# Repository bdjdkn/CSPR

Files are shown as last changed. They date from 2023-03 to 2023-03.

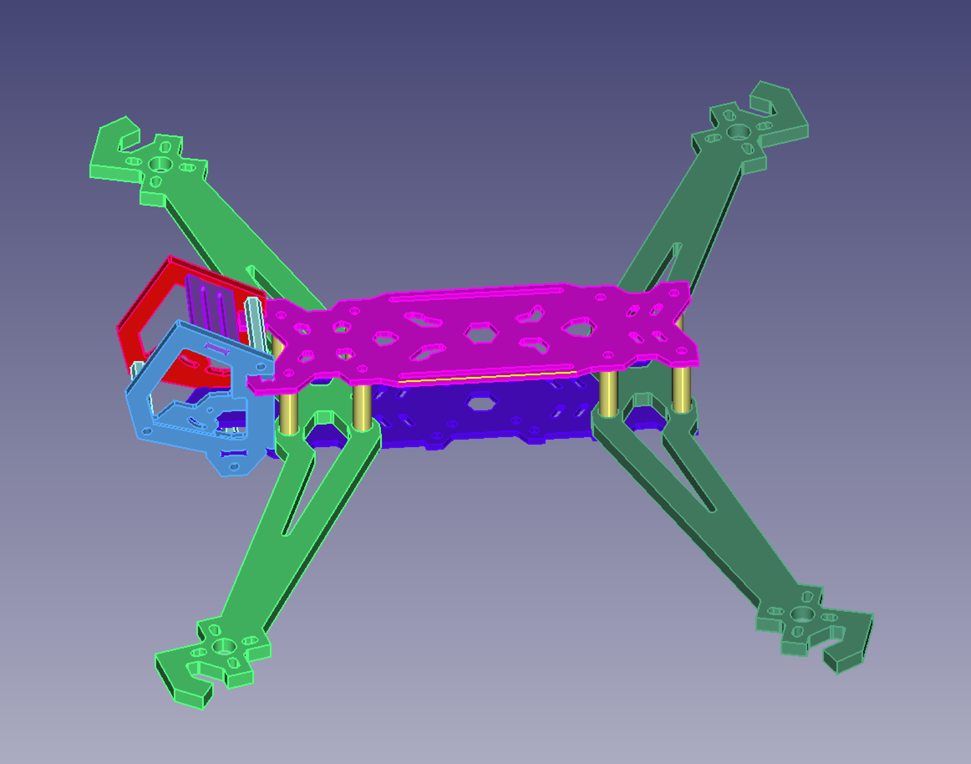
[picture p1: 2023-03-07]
图纸与模型/模型/动平台四代/参考资料/iflight-hl7-1.snapshot.7/2.png

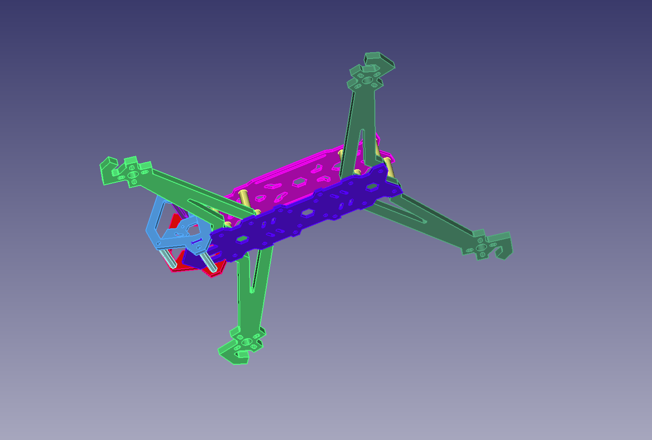
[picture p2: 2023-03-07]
图纸与模型/模型/动平台四代/参考资料/iflight-hl7-1.snapshot.7/3.png

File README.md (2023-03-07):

# CSPR
a machine with rope_driven  
这是一个四电机四卷筒的绳驱动系统，包含了机械设计部分和控制性文件，还在更新中，尚未完成  
This is a system which is combine with four rolls,the repository included the design of machine and part of controling code.the project is still updating  
RECODE  
22_6 creat the project and start to design  
22_12 finished the machine design and start to design the software  
23_2 finished the combine of the machine

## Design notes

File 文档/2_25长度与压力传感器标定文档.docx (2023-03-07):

# 长度与压力标定

1、 长度标定

目的：测量长度与卷筒旋转角度的关系，是否符合设计需求

测量方法：使用DJI Assistant软件位置环控制电机。

1、 上电前双手拉紧绳子，使卷筒保持初始位置。
2、 上电并使用PWM接口，杜邦线带金属眼端朝上插入FT232芯片的串口转换器
3、 打开DJI Assistant1.9软件，软件将识别电机，进入控制模式
4、 更改为位置环控制，电机将上电初始位置设置为0点
5、 确保电机出于0点位置，并使绳子稍微绷紧（过大的力量将会改变卷筒位置），并使用软件让电机转动一圈
6、 用记号笔在出绳点附近的绳上涂抹一端
7、 使用控制软件让电机转回一圈
8、 稍微绷紧绳子，观察电机数据，保持0点
9、 测量出绳点到记号的距离并记录
10、 同样的方法测量半圈的长度，并记录

测量数据：

出绳标号 | 一圈数据（理想为502.65mm） | 半圈数据（理想为251.32mm）
B1-1
B1-2
B2-1
B2-2
B3-1
B3-2
B4-1
B4-2

2、 压力标定

目的：校准压力传感器，减少偏差

测量方法：

1、 打开MATLAB setting_2_4
2、 依据软件提示完成配置
3、 打开simulink real_time_2_4
4、 测试不同重量下的读书，是否准确

Ps：标定零点时要确保绳子处于伸直状态且无重物挂载，标定选择对的通道，且重物稳定不晃动

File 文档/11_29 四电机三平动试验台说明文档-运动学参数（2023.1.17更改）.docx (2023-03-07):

# 四电机三平动试验台说明文档

编写人：项升 张胤启 22/11/30

文档使用软件：绘图Visio AxGlyph 公式 Axmath

2023/1/17 进行完善，更改了运动学参数和图片，完善了电气布置

## 1运动学参数和零件编号

下图1-1采取从控制电脑向架子（向北视角），对1）电机can地址拨码编号，贴纸（1-7， 现有电机为1-4 新电机是 5 6） 2底板编号（1-4），出绳臂编号（1.1 1.2 -4.1 -），贴纸。

图1-1 硬件编号规则

红色（1）短 绿色长（3）

Bx 635mm min：285mm max：785mm 每50mm为一节

By 555mm min：255mm max：655mm 每50mm为一节

坐标： | Bx（mm） | By（mm）
B11 | 317.5（可调） | -112.5
B12 | 317.5（可调） | 112.5
B21 | 137.5 | 277.5（可调）
B22 | -137.2 | 277.5（可调）
B31 | -317.5（可调） | 112.5
B32 | -317.5（可调） | -112.5
B41 | -137.5 | -277.5（可调）
B42 | 137.5 | -277.5（可调）

%%%%

需要给出B11-B42的三维可调离散集合(是由铝底板和机械设计确定的)表格（不改变O前提下）

| (m)（可调 X Y） | z (m) 以铝板上表面为原点，向上正值 | Bi1 -Bi2间距
B11 B12
B21 B22
B31 B32
B41 B42

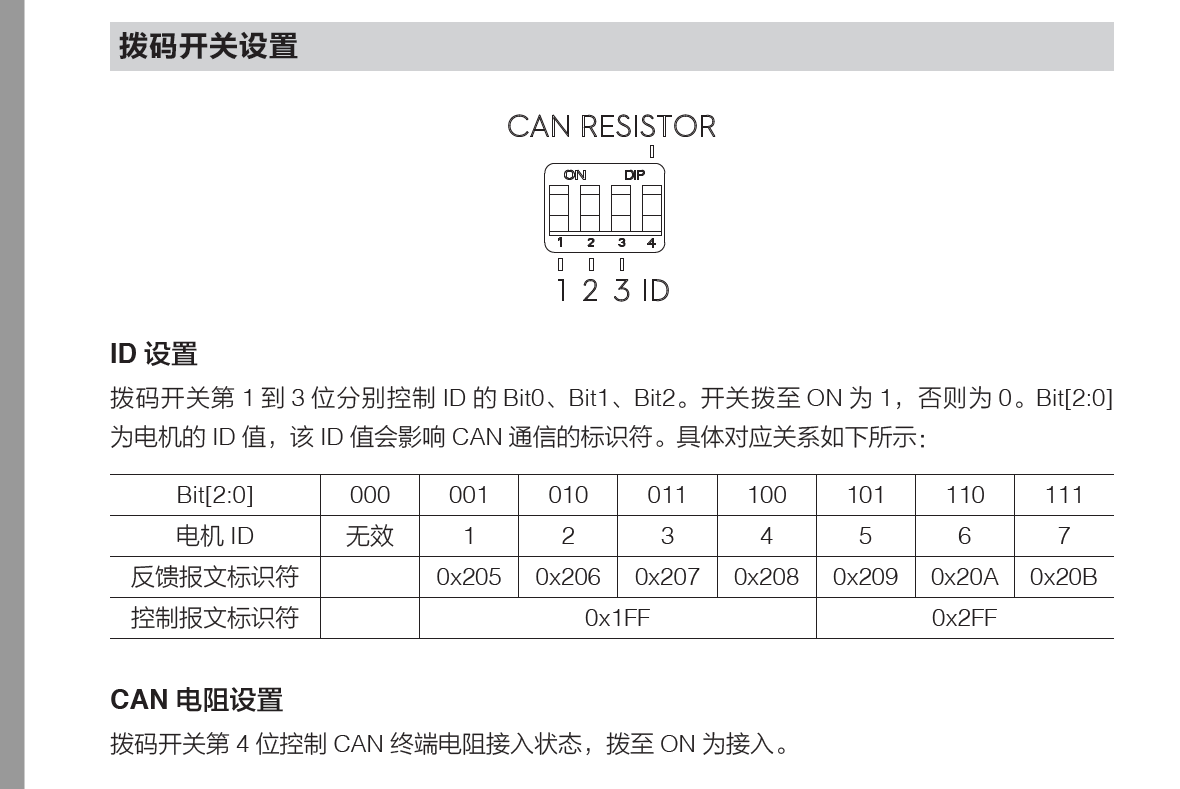
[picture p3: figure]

Dji 6020 电机： 注意CAN回路电阻有要求，最后测试。

%%%%

未完成，需要修改本图（注意出绳点B坐标系原点选择在B围成的几何中心。出绳点B可调范围，规则）

表4-1 六自由度CSPR出绳点和动平台系绳点的坐标

Table 4-1 Coordinates of the cable attachment points of the six DOF CSPR

| (m)（可调） | (m)
1
2
3
4
5
6

## 3 动平台开发

基本参数：225*275

结构：臂、结构板、主控小盒、铝柱、执行板

设计思路：

模型：

### 3.1 机械连接

1. 拉力组件的组装

1.1 拉力组件与c型板连接用超扁头M6*8螺丝上紧，保证凸台位于外侧并与拉力连接组件贴合。

1.2取下两个对应的垫片，用4.0的钻头进行扩孔，保证M4螺丝可自由穿过。

1.3用锉刀打磨垫片使其表面较为光滑并且能和滑轮较为顺滑的塞入C板中间。

1.4按照垫片 滑轮 垫片的顺序进行组装并把孔位对其，用滑轮自带的M4螺丝从无凸台一侧插入，转入有凸台一侧的螺纹孔

2. 小L板的组装

2.1取下对应的垫片并进行扩孔

2.2安装到小L板外侧

2.3把万向轮从有沉孔的一侧插入并从内侧拧上螺母，保证万向轮的进绳孔较为水平。

3. 最后组装

3.1先将柱塞螺丝塞入大L板通孔内，然后将拉力组件用M6*8超扁头螺丝与大L板固定，且保证螺丝头不突出，拉力计与台面对齐。

3.2柱塞螺丝与定位板上紧

3.3依次把小L板和剩下的滑轮安装上去

3.4调整滑轮方向，第一个入绳滑轮，方向向上，第二个拉力滑轮方向向外（小板方向）第三个滑轮方向朝上

线的画法

槽的设计

### 3.2电气和控制系统

IMU系统测试与开发：

匿名透传模块测试：

使用MATLAB在desktop real—time上进行4*double+8*int8进行收发sin波函数，通过观察图形，能完成200kz的通讯任务。

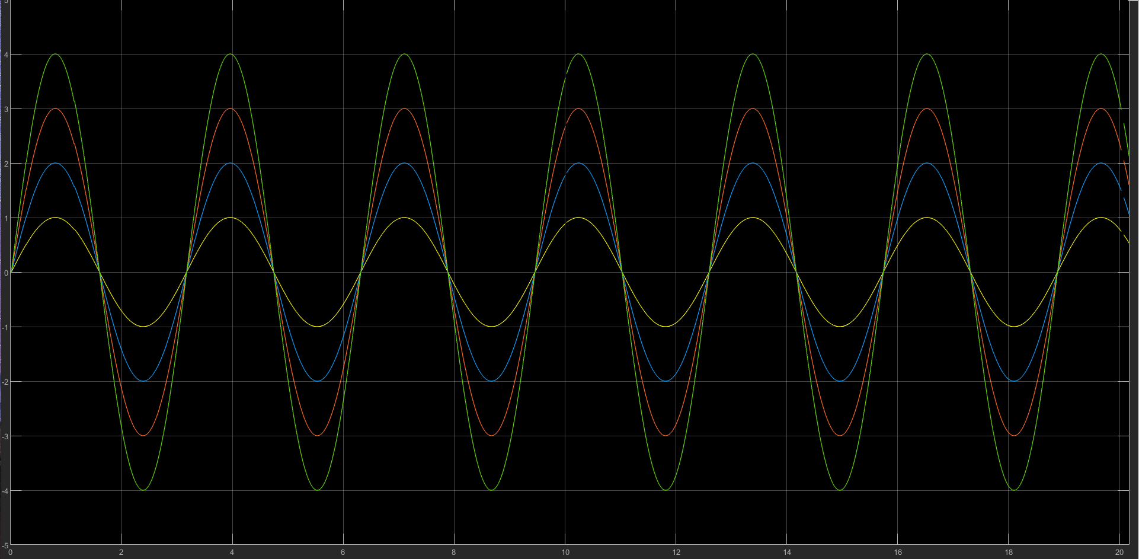
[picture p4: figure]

接受的图像和发送图像一致

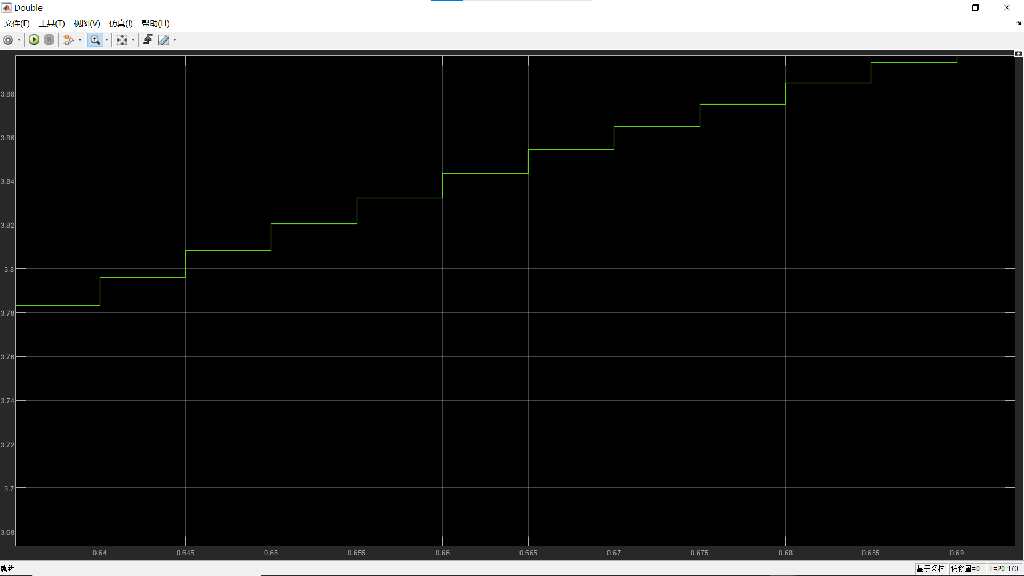
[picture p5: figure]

放大观察每个数据符合200hz的设定

自定义ping

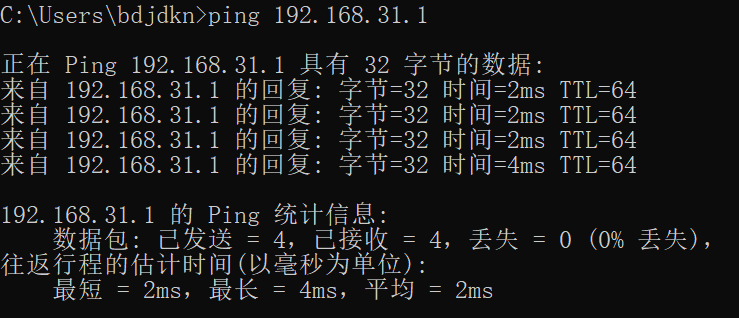
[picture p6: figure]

Ping路由器的延迟（有线无线结果相同）

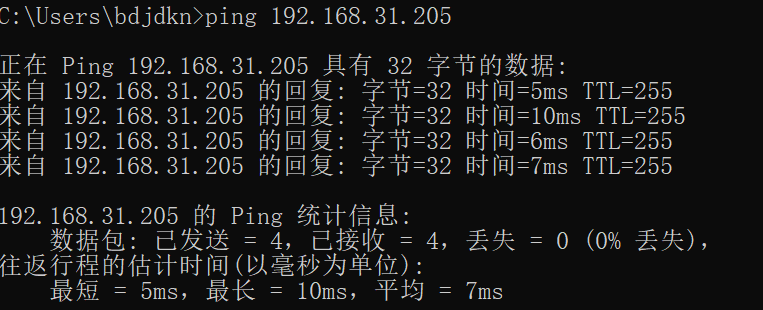
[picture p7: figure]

Ping透传模块的延迟%第一次ping出现一次116ms延迟（无线）

透传模块长时间没用第一次延迟普遍偏高？？？需要改变测试的网络环境重新测试

%%%是否需要在开启系统前传输一个没有意义的包激活透传模块来减少第一次的大延迟以防止出现数据堵塞（需要测试）

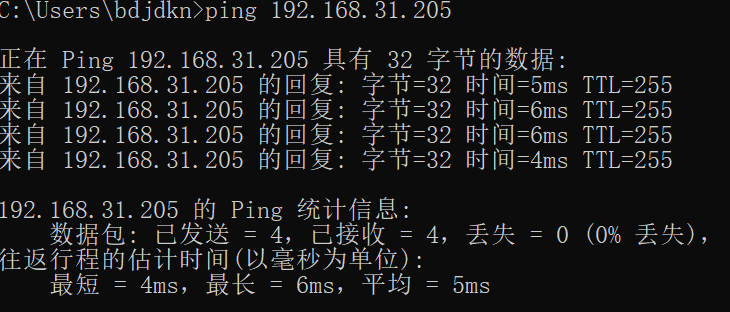
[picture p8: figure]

Ping透传模块的延迟（有线）

IMU读取任务：

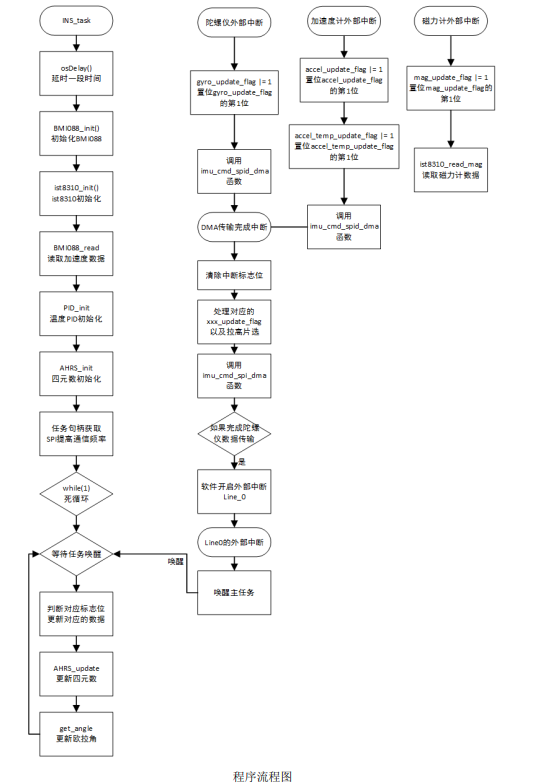
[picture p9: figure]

缝合DJI_example中的11/13/16/18开发IMU系统，通过串口将欧拉角传输到匿名模块发送给上位机，上位机。（是否需要温度PID来控制温漂的问题？）

测试系统性能：

1、 开发板通过定时器向上位机发送sin波函数，上位机读取同时也向开发板发送sin波函数，开发板将接受到的数据通过串口在上位机上进行绘图，观察四个数据是否有出入，整个系统能否完成200hz的运作
2、 开发板读取BMI088和IST8310的频率，以及更新欧拉角的频率，能否满足通信系统需要的200hz
3、 每一个数据帧打上时间戳，测试整个系统的延迟

## 2电机、传感器和主控制系统

### 2.1电气接线图

八个压力传感器，每四个为一组，连接变送器。压力传感器的线从定位板的孔穿出，变送器卡在安装导轨上，安装导轨通过螺丝与定位板相连，多余的线束用扎带困好，每个变送器占用四根线，两根485信号线，两根电源线。总共8根线。信号线用网线做线束，与变送器连接一端用冷压端子压住再与变送器连接。网线进过机架，在底部通过压线端子与485转换器相连，在传输到电脑上。电源线使用硅胶线与xt30相连，进入分线器。分线器通过打印的转换板与定位板相连。

电机的通过CAN进行通信，所有的电机can先通过硅胶线与分线器相连，分线器再与网线的两根线相连，最后通过can-usb进入电脑。

### 2.2零部件列表

电机支架*4

轮组*4

大L板*8

小L板中*8（左右各四）

NT002*24

拉力传感器*8

C型连接件*8

万向轮*8

## 4 控制算法开发

### 4.1和上位机simulink 的连接

4.1.1 压力传感器连接

1、MATLAB使用脚本设置变送器参数并启动连续发射模式

%两个四路数字变送器设置文件

%2023.1.2 张胤启

% 1、设置变送器 状态1.1：设置零点 状态1.2：标定量程比例系数

% 2、连续发送的状态

% 3、接收一帧确认进入连续发送状态

% 4、返回成功的命令

%%%%%%%%%%%%%%%%%%%%%%%%%%%

clear;%清除所有内容

txt="请核对串口信息";

disp(txt);

scom1= serialport('COM3',115200);%配置第一个变送器的串口

scom2= serialport('COM12',115200);%配置第二个变送器的串口

disp(scom1);

disp(scom2);

flush(scom1);%清除1号缓冲区

flush(scom2);%清除2号缓冲区

%%%%%%%%%%%%%%%%%%%%%%%%%%%

txt="请设置模块参数,默认更改所有通道的参数";

disp(txt);

txt="AD转换速率 0x00:10 0x01:40 0x02:640 0x03:不更改";

AD=input(txt);

right=[0xFE,0x01,0xF2,0x01,0xCF,0xFC,0xCC,0xFF];

if AD~=0x03

txt="设置极性 0x00:双向;0x01:单向 默认单向";

Polay=input(txt);

data(:,1)=[0xFE,0x01,0x21,0xFF,AD,Polay,0xCF,0xFC,0xCC,0xFF];

write(scom1,data,"uint8");

write(scom2,data,"uint8");

back_AD1=read(scom1,8,"uint8");

back_AD2=read(scom2,8,"uint8");

if back_AD1==right

txt="一号设置成功";

disp(txt);

end

if back_AD2==right

txt="二号设置成功";

disp(txt);

end

end

%%%%%%%%%%%%%%%%%%%%%%%%%%%

txt="滤波器设置";

disp(txt);

txt="滤波方式";

disp(txt);

txt="0x00:不使用 0x01:平均值滤波";

disp(txt);

txt="0x02:中位值滤波 0x03:一阶滤波";

disp(txt);

txt="0x04:滑动平均滤波 0x05:中位值平均滤波";

disp(txt);

txt="0x06:滑动中位值平均滤波";

disp(txt);

txt="0x07:平均值滤波 + 一阶滤波";

disp(txt);

txt="0x08:中位值滤波 + 一阶滤波";

disp(txt);

txt="0x09:滑动平均滤波 + 一阶滤波";

disp(txt);

txt="0x0A:中位值平均滤波 + 一阶滤";

disp(txt);

txt="0x10不更改";

lvbo=input(txt);

if lvbo~=0x10

txt="范围：0~50，数字越大，滤波越强 ";

level=input(txt);

data(:,1)=[0xFE,0x01,0x22,0xFF,lvbo,level,0xCF,0xFC,0xCC,0xFF];

write(scom1,data,"uint8");

write(scom2,data,"uint8");

back_lvbo1=read(scom1,8,"uint8");

back_lvbo2=read(scom2,8,"uint8");

if back_lvbo1==right

txt="一号设置成功";

disp(txt);

end

if back_lvbo2==right

txt="二号设置成功";

disp(txt);

end

end

%%%%%%%%%%%%%%%%%%%%%%%%%%%

txt="是否设置零点";

disp(txt);

txt="0x01 是 0x00 否";

zero=input(txt);

if zero==0x01

data_zero(:,1)=[0xFE,0x01,0x30,0xFF,0x00,0x00,0x00,0x00,0xCF,0xFC,0xCC,0xFF];

write(scom1,data_zero,"uint8");

write(scom2,data_zero,"uint8");

back_zero1=read(scom1,8,"uint8");

back_zero2=read(scom2,8,"uint8");

if back_zero1==right

txt="一号设置成功";

disp(txt);

end

if back_zero2==right

txt="二号设置成功";

disp(txt);

end

end

%%%%%%%%%%%%%%%%%%%%%%%%%%%

txt="连续发送设置";

disp(txt);

txt="延迟设置 16进制 单位ms 不应小于5ms，小于5ms，会造成一定的数据帧破损";

delay=input(txt);

txt="数据类型;0x00:测量值;0x01:AD 内码值;0x02:毛重值;0x03:净重值;0x04:峰值;0x05:谷值;0x06:峰谷差值";

datatype=input(txt);%数据类型;00:测量值;01:AD 内码值;02:毛重值;03:净重值;04:峰值;05:谷值;06:峰谷差值

txt="发送类型:0x00:不管数据有没有变化，都发送；0x01:只在数据变化时发送";

sandtype=input(txt);%发送类型:0x00:不管数据有没有变化，都发送；0x01:只在数据变化时发送

data_sand(:,1)=[0xFE,0x01,0x07,0xFF,0x01,datatype,sandtype,delay,0xCF,0xFC,0xCC,0xFF];

write(scom1,data_sand,"uint8");

back_sand1=read(scom1,8,"uint8");

write(scom2,data_sand,"uint8");

back_sand2=read(scom2,8,"uint8");

if back_sand1==right

txt="一号发送成功";

disp(txt);

end

if back_sand2==right

txt="二号发送成功";

disp(txt);

end

%%%%%%%%%%%%%%%%%%%%%%%%%%%%

clear;%清除所有内容 关闭串口

%更改相应设置需在下面更改

%变送器设置数据

%协议 自由协议

%波特率 115200

%地址 01

%校验 00不使用

%AD转换速率 640

%滤波 0x01 5

%重量单位 00 无

%最大重量和分度 10，000 0x09 0.1

2、通过simulink读取变松器的数据并进行解帧，进行绘图

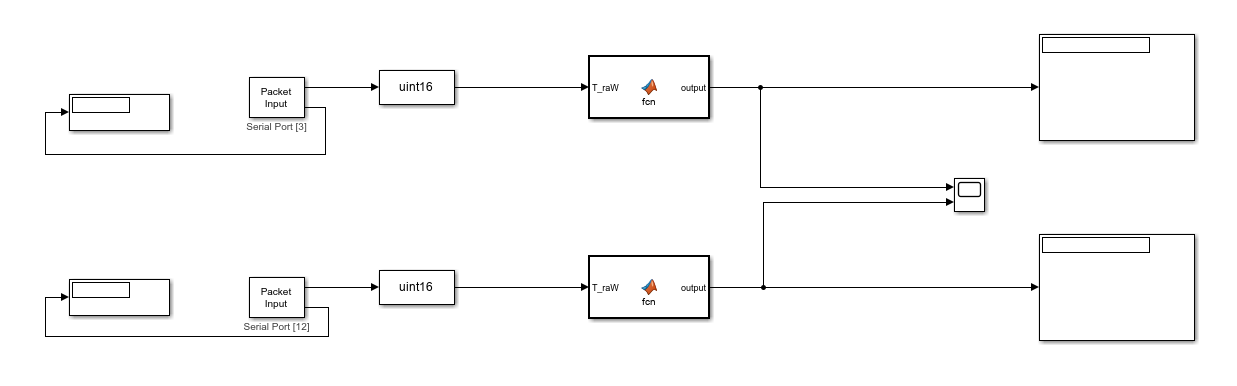
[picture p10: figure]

### 4.2 simulink中的控制算法模块实现

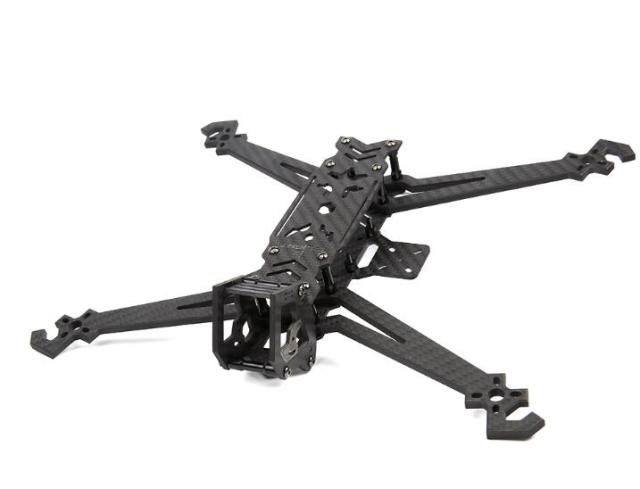
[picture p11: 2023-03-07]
图纸与模型/模型/动平台四代/参考资料/iflight-hl7-1.snapshot.7/iFlight-HL7-V2-296mm-7inch-Long-Range-FPV-Frame-kit-with-5mm-arm-compatible-gemfan-7042.jpg_640x640.jpg

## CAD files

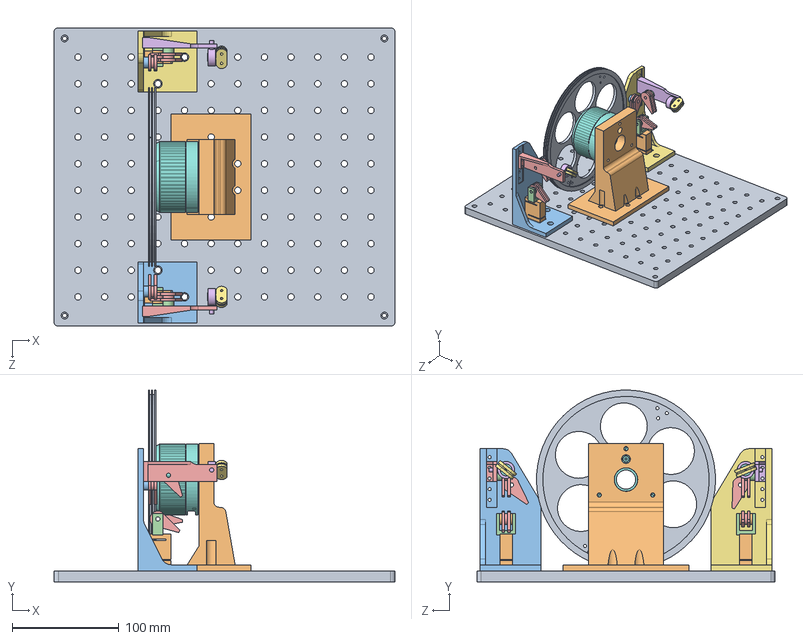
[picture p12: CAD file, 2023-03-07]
图纸与模型/模型/4轮平台张3.0（总）/板套装竖3.0.SLDASM
320.0 x 179.9 x 280.0 mm
定位板
拉力计 x 2
六角柱与拉力机连接板
拉力连接件 x 2
NT002滑轮 x 6
万向绳2 x 2
万向绳1 x 2
万向绳3 x 2
万向绳4 x 2
拉力计滑轮垫片 x 4
滑轮1垫片 x 2
滑轮2垫片 x 2
滑轮2连接板2.0
滑轮2连接板2.0右
六角柱与拉力机连接板右
RoboMaster GM6020 直流无刷电机
轮组2.0
电机固定3.0

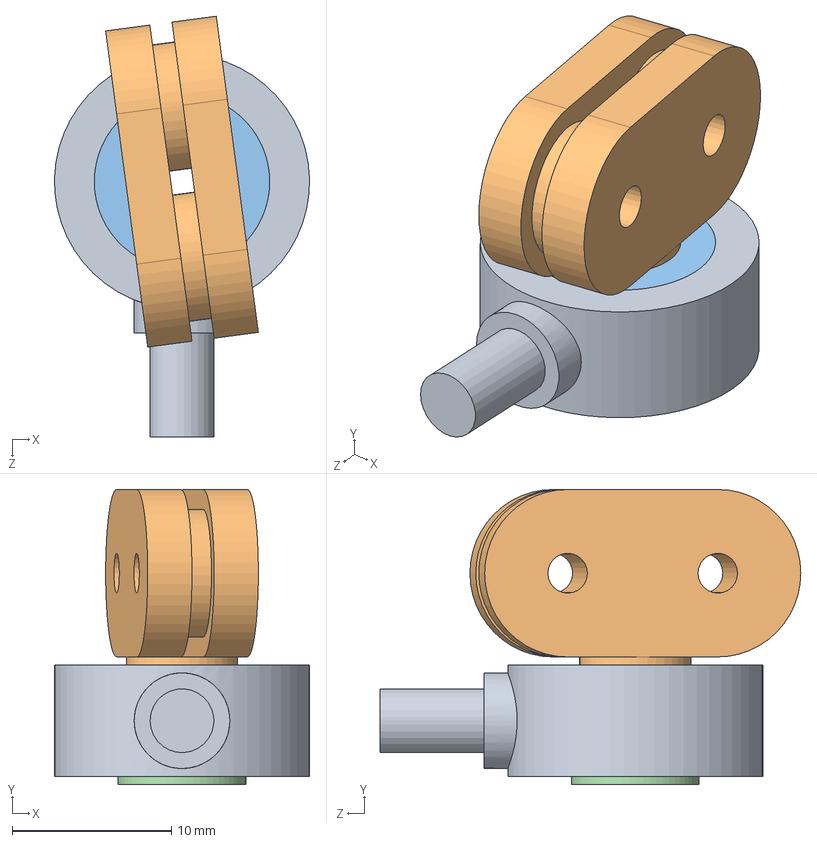
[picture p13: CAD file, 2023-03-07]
图纸与模型/模型/万向绳/万向绳.SLDASM
16.0 x 18.5 x 26.4 mm
万向绳2
万向绳1
万向绳3
万向绳4

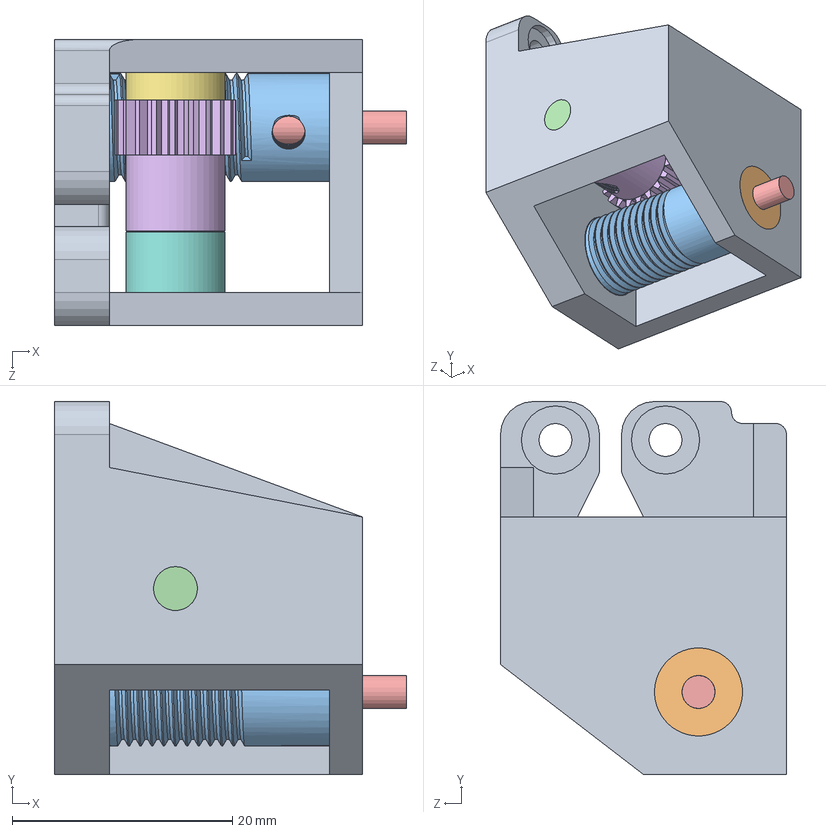
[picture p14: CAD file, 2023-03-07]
图纸与模型/模型/轮/绳长微调器/三维建模/装配体.SLDASM
32.0 x 33.9 x 26.0 mm
bearing x 2
零件2
zhou1
zhou2
gear

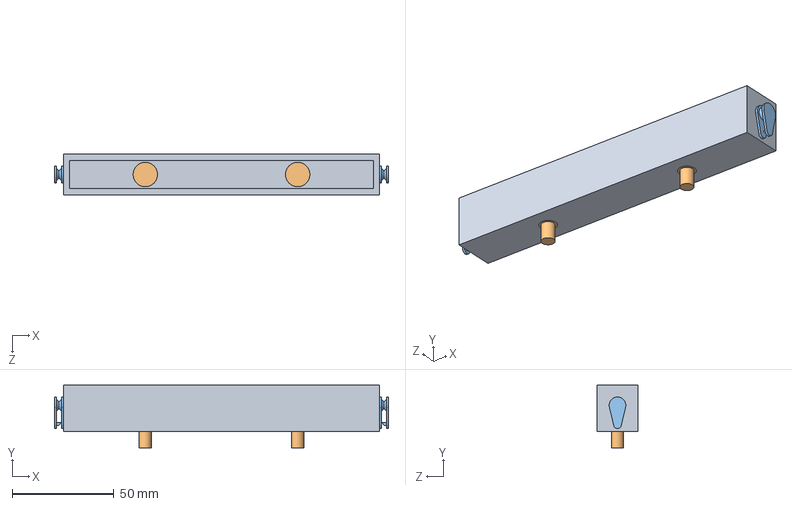
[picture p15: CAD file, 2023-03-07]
图纸与模型/模型/零件/出绳点链接板（150）.SLDASM
164.4 x 31.0 x 20.0 mm
出绳点链接板（150）
柱塞螺丝M6 x 2
零件1^latest1 x 2

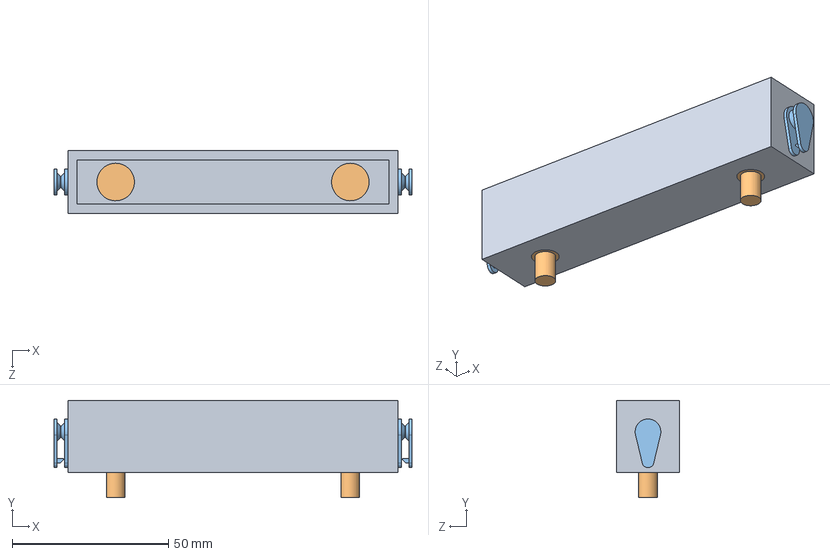
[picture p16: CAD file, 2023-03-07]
图纸与模型/模型/万向绳/万向件/出绳点链接板（万向件）.SLDASM
114.4 x 31.0 x 20.0 mm
出绳点链接板（100）
柱塞螺丝M6 x 2
零件1^latest1 x 2

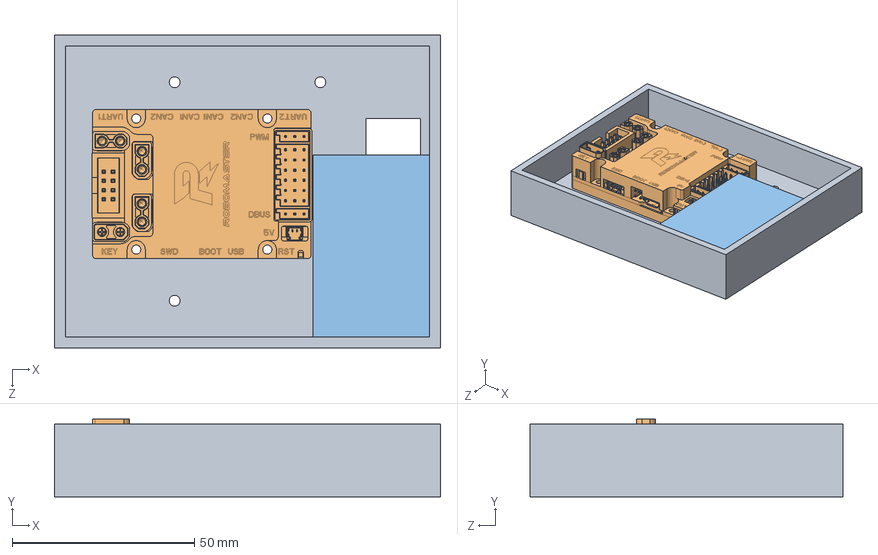
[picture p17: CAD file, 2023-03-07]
图纸与模型/模型/动平台四代/控制盒/控制盒装配体.SLDASM
106.0 x 21.3 x 86.0 mm
控制盒1.0
DJI_C
匿名透传（简）

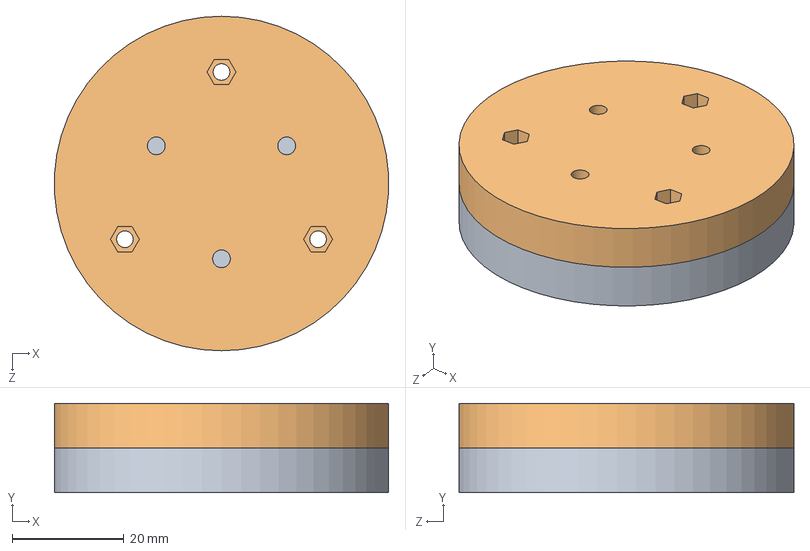
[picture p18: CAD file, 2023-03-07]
图纸与模型/模型/测试平台/转换口.SLDASM
59.9 x 16.0 x 60.0 mm
转换口卷筒一侧
转换口电机一侧

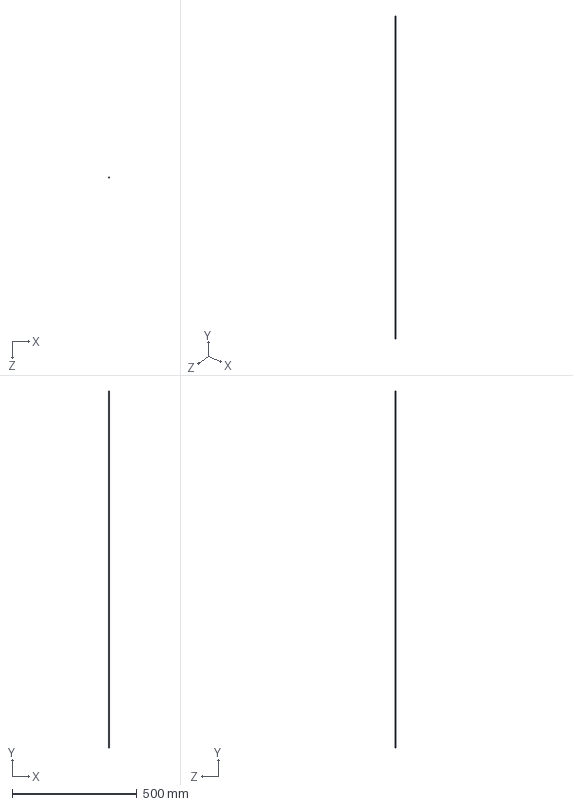
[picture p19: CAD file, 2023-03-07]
图纸与模型/模型/绳/绳组合.SLDASM
2.00 x 1430.5 x 2.00 mm
绳2 x 2

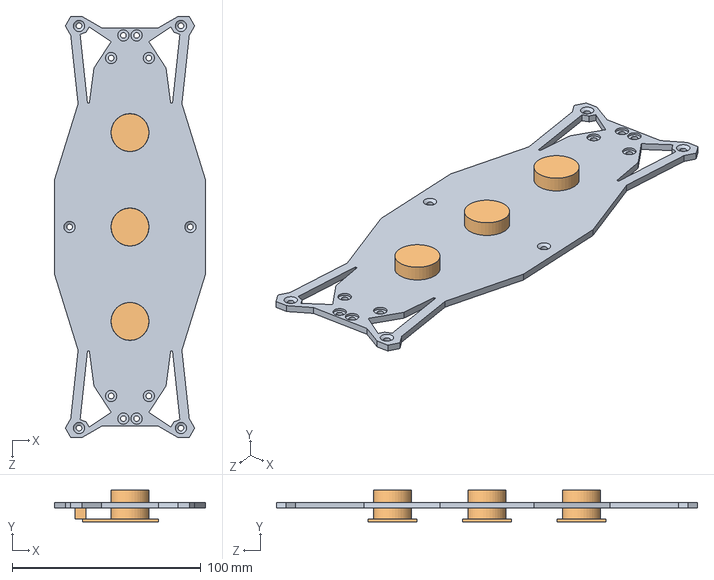
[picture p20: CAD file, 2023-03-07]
图纸与模型/模型/动平台四代/执行板_电磁铁/执行板_电磁铁1.0.SLDASM
80.0 x 16.8 x 223.0 mm
执行板
电磁铁 x 3

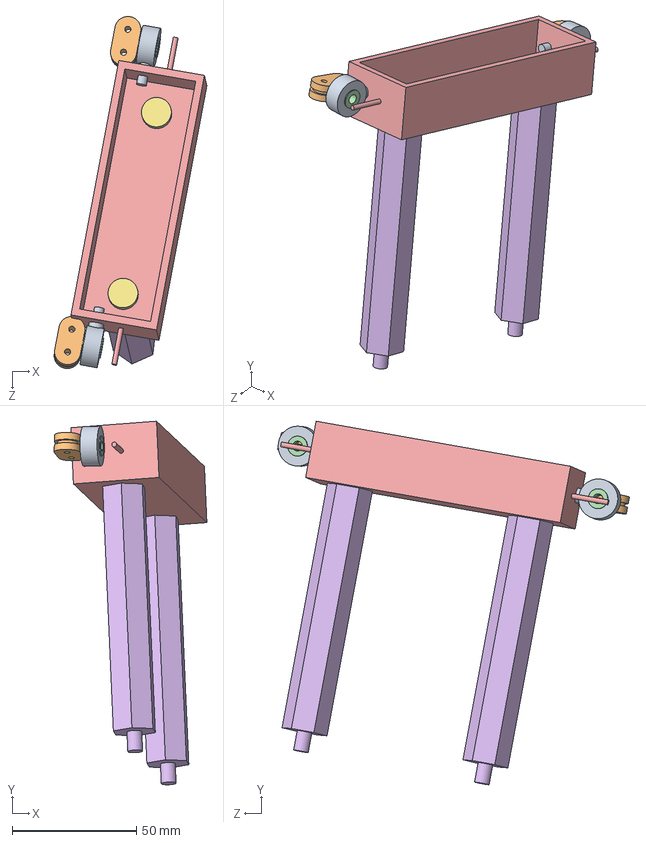
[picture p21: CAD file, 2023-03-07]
图纸与模型/模型/万向绳/万向件/装配体2.SLDASM
61.4 x 146.0 x 141.4 mm
万向绳2 x 2
万向绳1 x 2
万向绳3 x 2
万向绳4 x 2
出绳点链接板（06.04）
单头六角柱100 x 2
柱塞螺丝M6 x 2

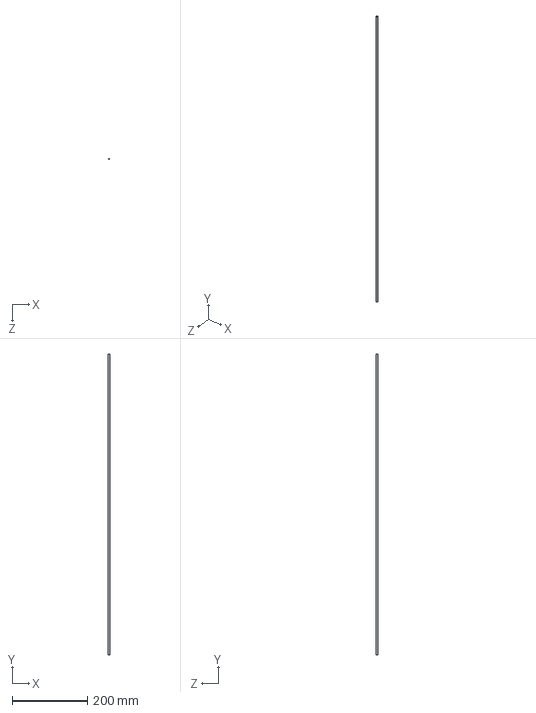
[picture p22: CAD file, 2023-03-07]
图纸与模型/模型/绳/绳组合2.0.SLDASM
4.00 x 800.0 x 4.00 mm

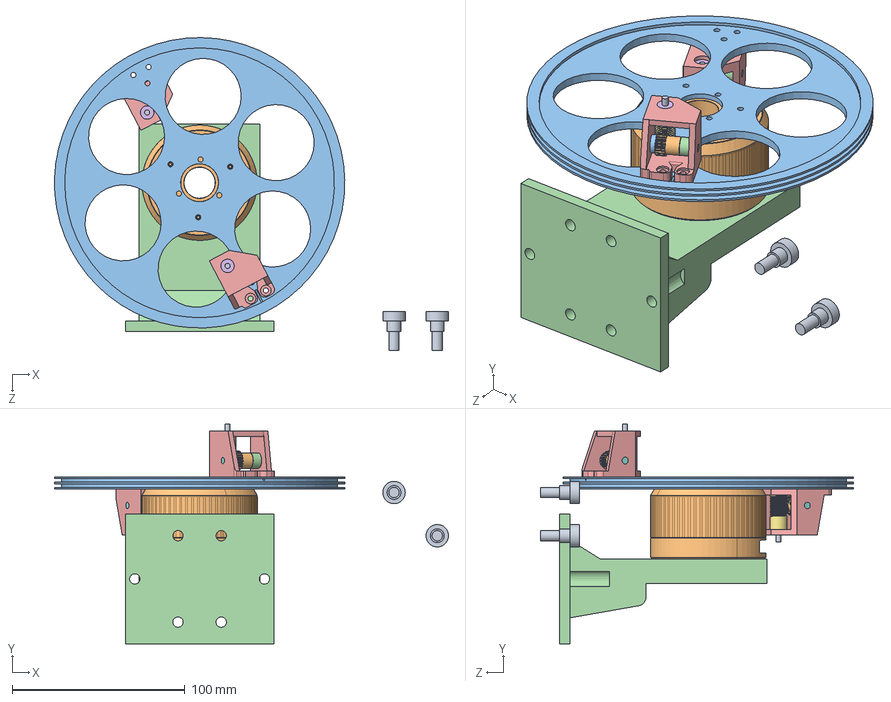
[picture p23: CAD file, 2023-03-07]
图纸与模型/模型/4轮平台张3.0（总）/板套装3.0.SLDASM
228.0 x 127.0 x 181.0 mm
塞打螺丝M6_5 x 2
RoboMaster GM6020 直流无刷电机
轮组2.0
电机固定3.0
bearing x 4
零件2 x 2
zhou1 x 2
zhou2 x 2
gear x 2

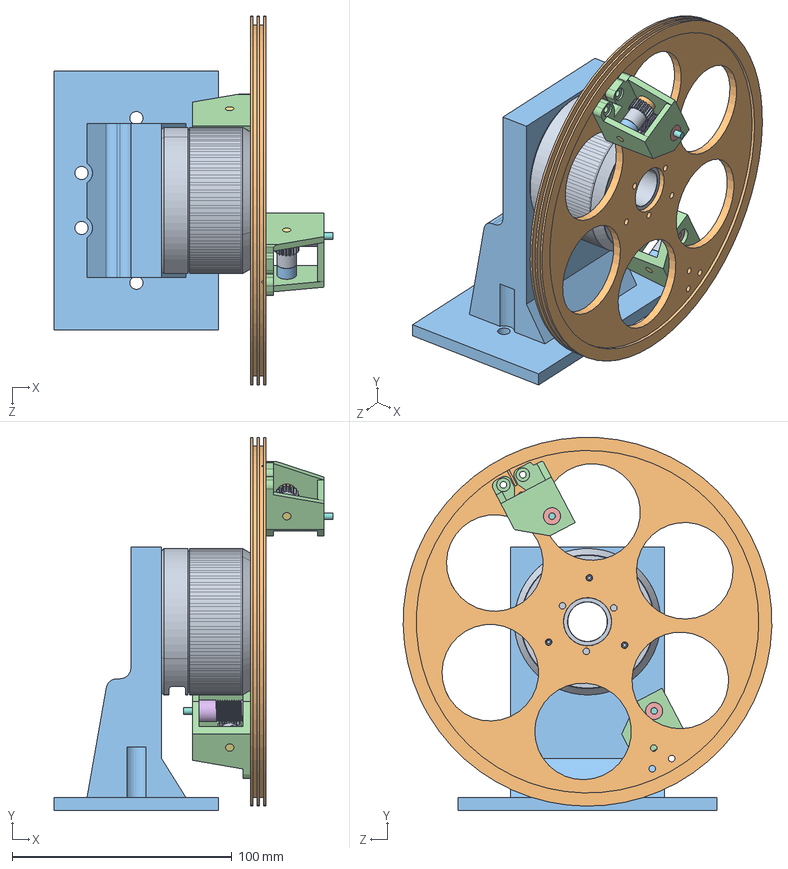
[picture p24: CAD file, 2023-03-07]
图纸与模型/模型/4轮平台张3.0（总）/电机固定组件3.0.SLDASM
127.0 x 169.9 x 167.9 mm
RoboMaster GM6020 直流无刷电机
轮组2.0
电机固定3.0
bearing x 4
零件2 x 2
zhou1 x 2
zhou2 x 2
gear x 2

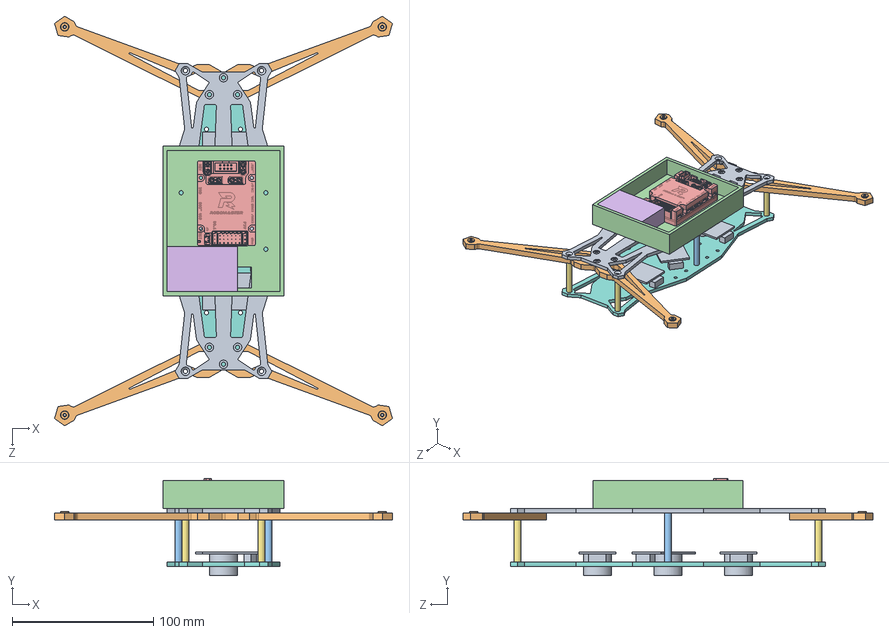
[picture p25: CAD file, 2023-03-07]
图纸与模型/模型/动平台四代/动平台四代1.0.SLDASM
239.4 x 68.8 x 290.1 mm
结构板
臂1.0 x 2
铝柱_35 x 2
控制盒1.0
DJI_C
匿名透传（简）
铝柱_30 x 4
执行板
电磁铁 x 3
瓷眼 x 4

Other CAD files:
图纸与模型/模型/4轮平台张3.0（总）/板套装右3.0.SLDASM
图纸与模型/模型/4轮平台张3.0（总）/板套装竖 _右3.0.SLDASM
图纸与模型/模型/零件/出绳点链接板（100）.SLDASM
图纸与模型/模型/万向绳/万向件/装配体3.SLDASM
图纸与模型/图纸/加工工程图3.0/六角柱与拉力机连接板.SLDDRW
图纸与模型/图纸/加工工程图3.0/六角柱与拉力机连接板右.SLDDRW
图纸与模型/图纸/加工工程图3.0/拉力连接件.SLDDRW
图纸与模型/图纸/加工工程图3.0/滑轮2连接板2.0.SLDDRW
图纸与模型/图纸/加工工程图3.0/滑轮2连接板2.0右.SLDDRW
图纸与模型/图纸/加工工程图3.0/轮组3.0.SLDDRW
图纸与模型/图纸/机加工投出定稿PDF版/加工包3.0PDF/六角柱与拉力机连接板.STEP
图纸与模型/图纸/机加工投出定稿PDF版/加工包3.0PDF/六角柱与拉力机连接板右.STEP
图纸与模型/图纸/机加工投出定稿PDF版/加工包3.0PDF/拉力连接件.STEP
图纸与模型/图纸/机加工投出定稿PDF版/加工包3.0PDF/滑轮2连接板2.0.STEP
图纸与模型/图纸/机加工投出定稿PDF版/加工包3.0PDF/滑轮2连接板2.0右.STEP
图纸与模型/图纸/机加工投出定稿PDF版/加工包3.0PDF/轮组3.0.STEP
图纸与模型/图纸/电机固定3.0.STL
图纸与模型/图纸/碳纤维加工/碳纤维加工投出定稿/执行板.DWG
图纸与模型/图纸/碳纤维加工/碳纤维加工投出定稿/执行板.STEP
图纸与模型/图纸/碳纤维加工/碳纤维加工投出定稿/结构板.DWG
图纸与模型/图纸/碳纤维加工/碳纤维加工投出定稿/结构板.STEP
图纸与模型/图纸/碳纤维加工/碳纤维加工投出定稿/臂1.0（2个）.DWG
图纸与模型/图纸/碳纤维加工/碳纤维加工投出定稿/臂1.0（2个）.STEP
图纸与模型/图纸/碳纤维加工/碳纤维图纸/执行板.SLDDRW
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

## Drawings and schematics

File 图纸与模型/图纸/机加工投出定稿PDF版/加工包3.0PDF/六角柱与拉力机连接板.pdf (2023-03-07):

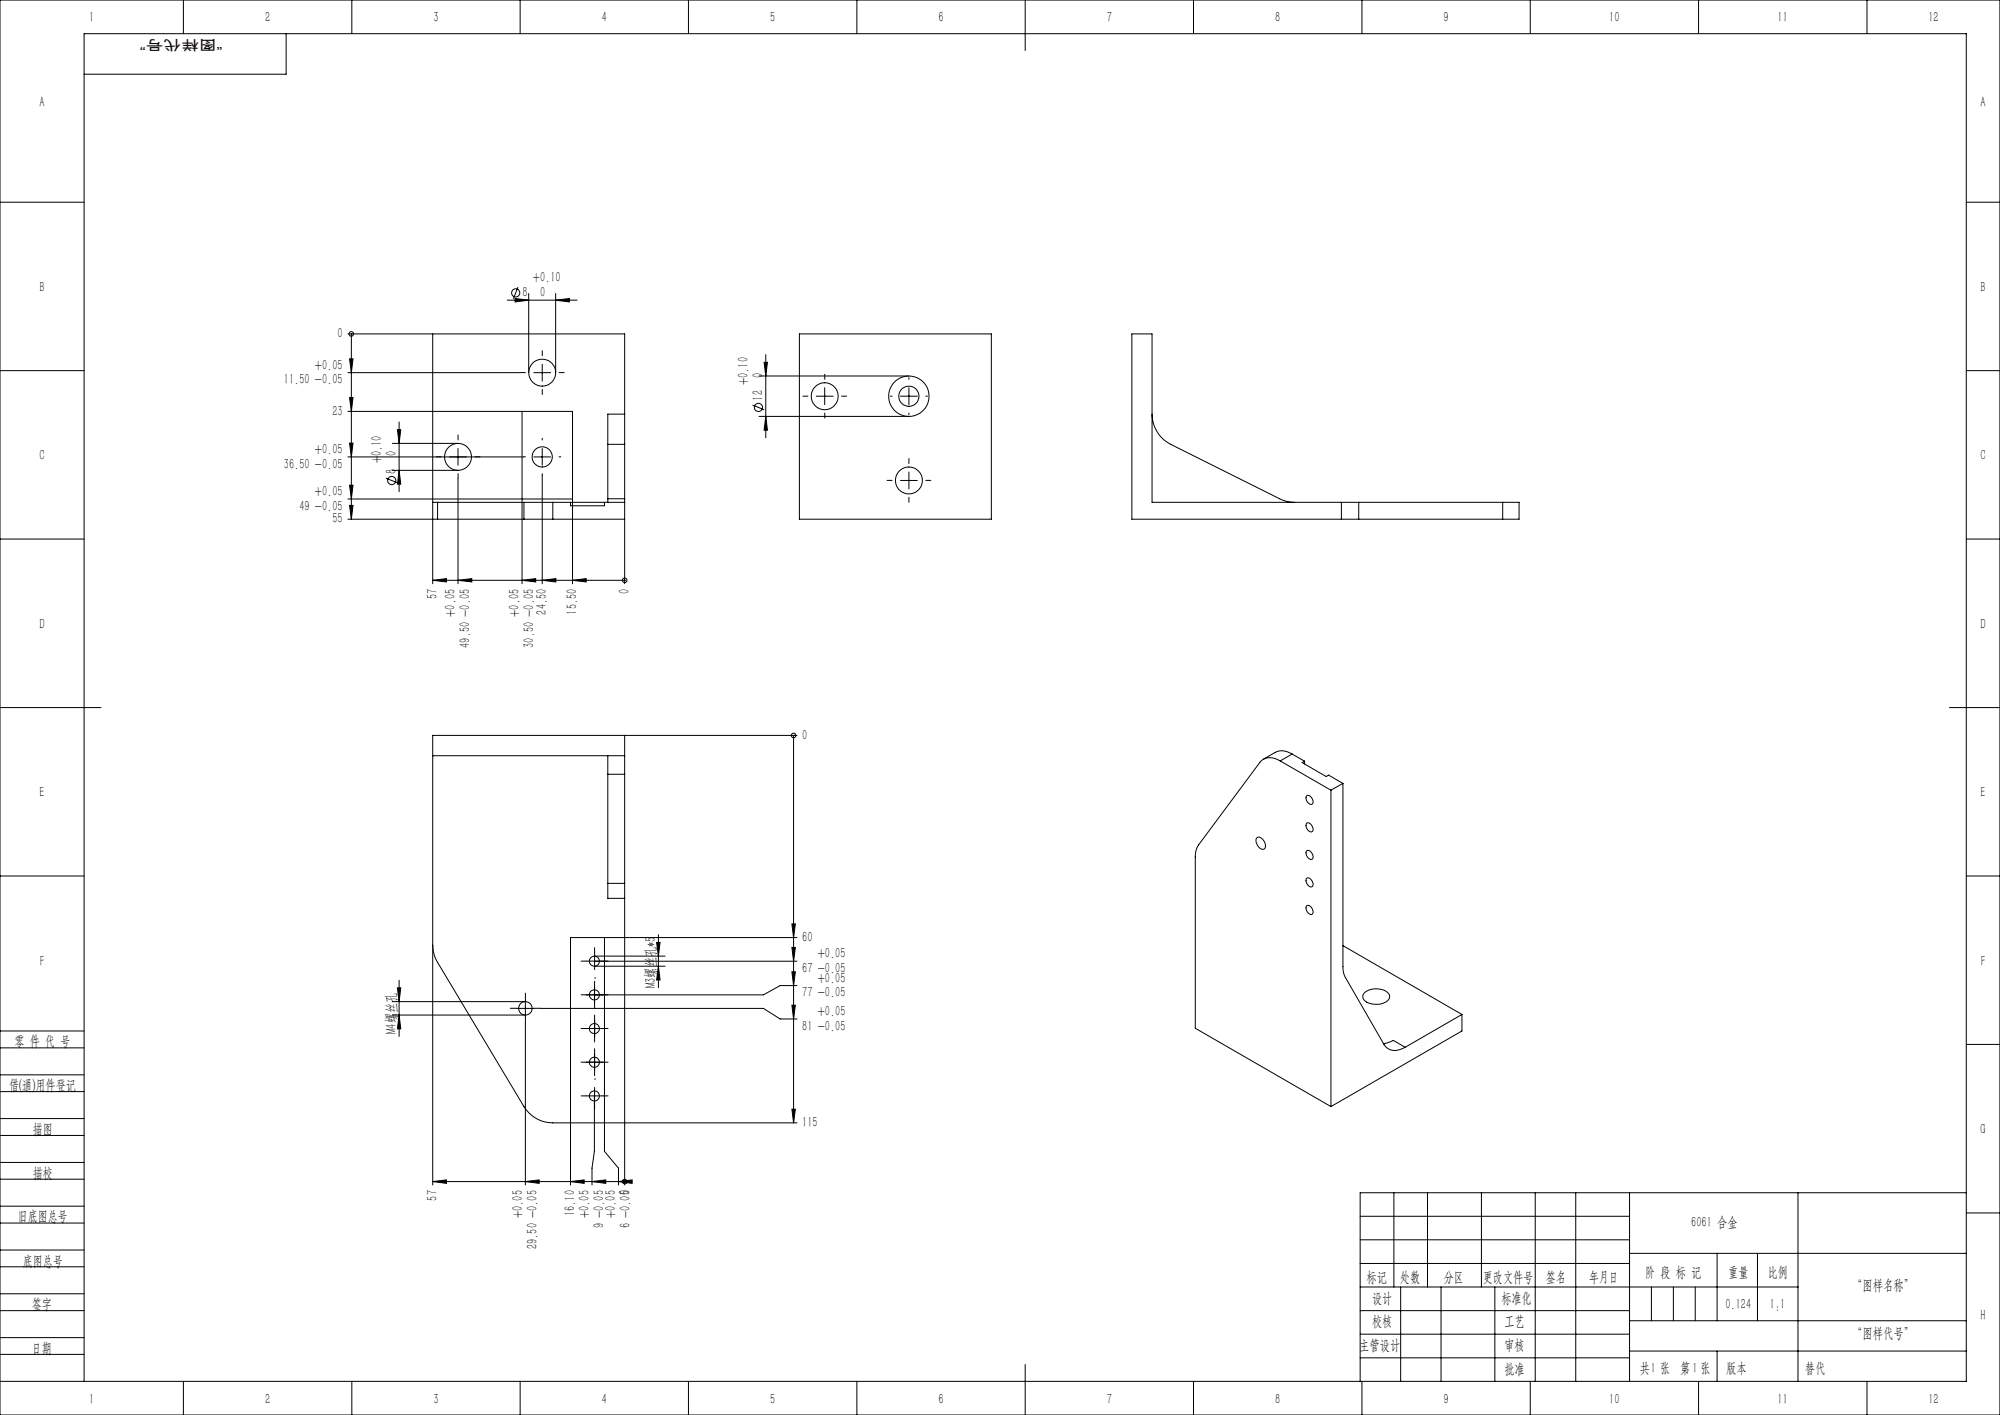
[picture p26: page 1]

阶 段 标 记 | 重量 | 比例 | “图样名称”

标记 | 处数 | 分区 | 更改文件号 | 签名 | 年月日
设计 | | | 标准化 | | | 0.124 | 1:1
校核 | | | 工艺

“图样代号”

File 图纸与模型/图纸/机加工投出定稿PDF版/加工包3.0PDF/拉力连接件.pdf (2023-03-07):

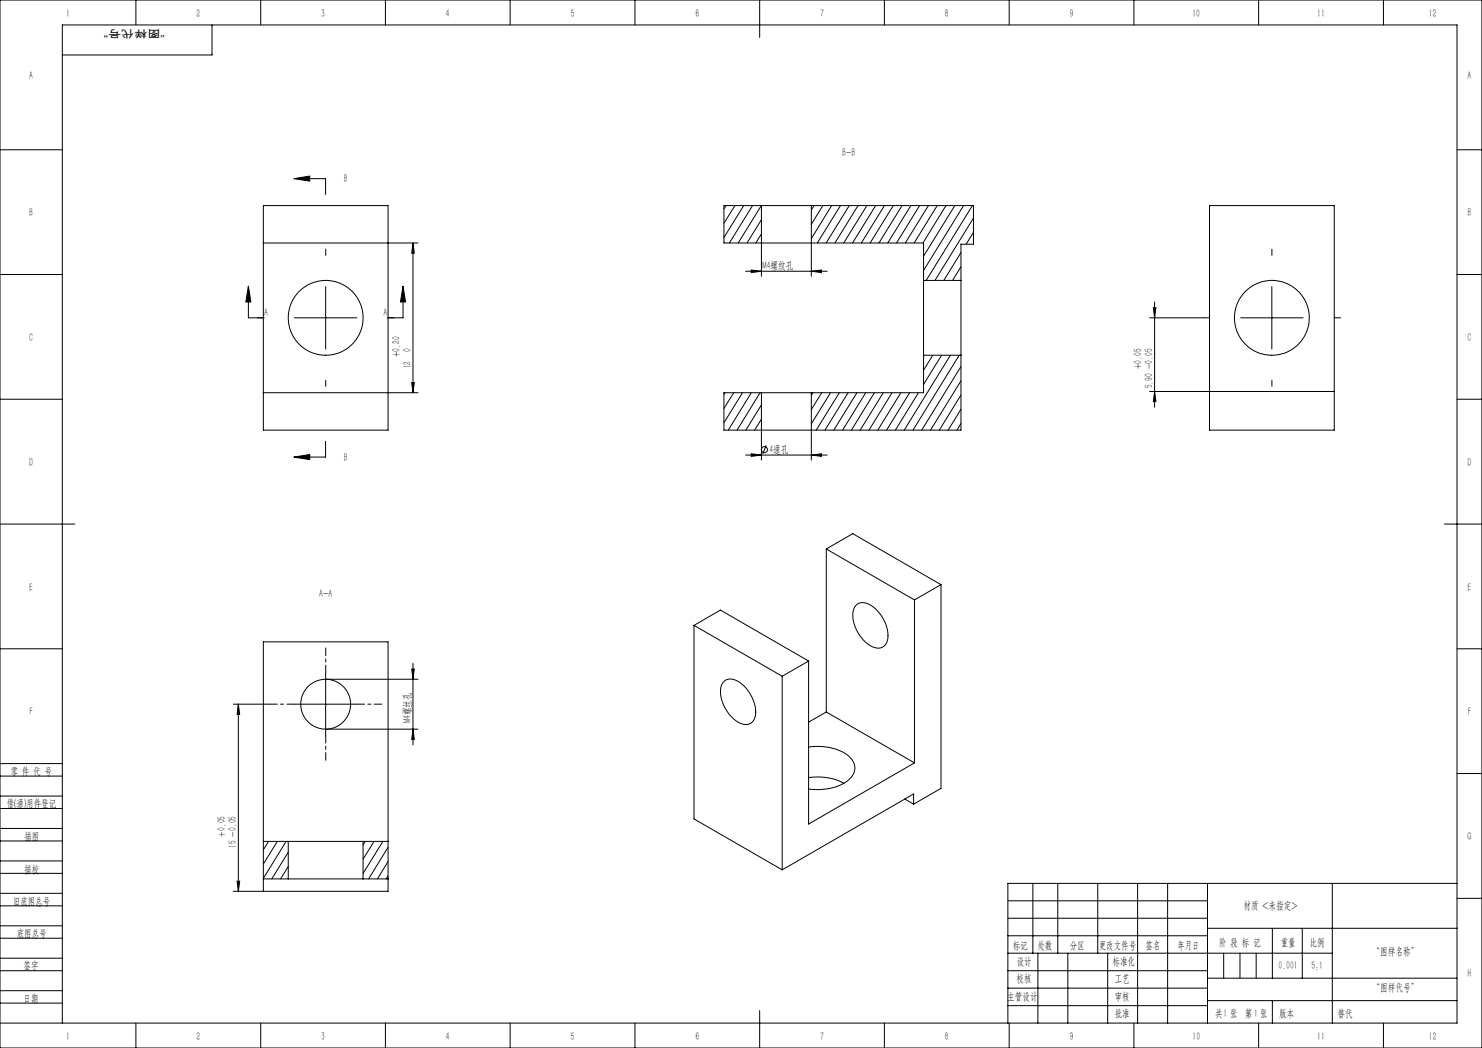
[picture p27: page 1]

材质 <未指定>

阶 段 标 记 | 重量 | 比例 | “图样名称”

标记 | 处数 | 分区 | 更改文件号 | 签名 | 年月日
设计 | | | 标准化 | | | 0.001 | 5:1
校核 | | | 工艺

“图样代号”

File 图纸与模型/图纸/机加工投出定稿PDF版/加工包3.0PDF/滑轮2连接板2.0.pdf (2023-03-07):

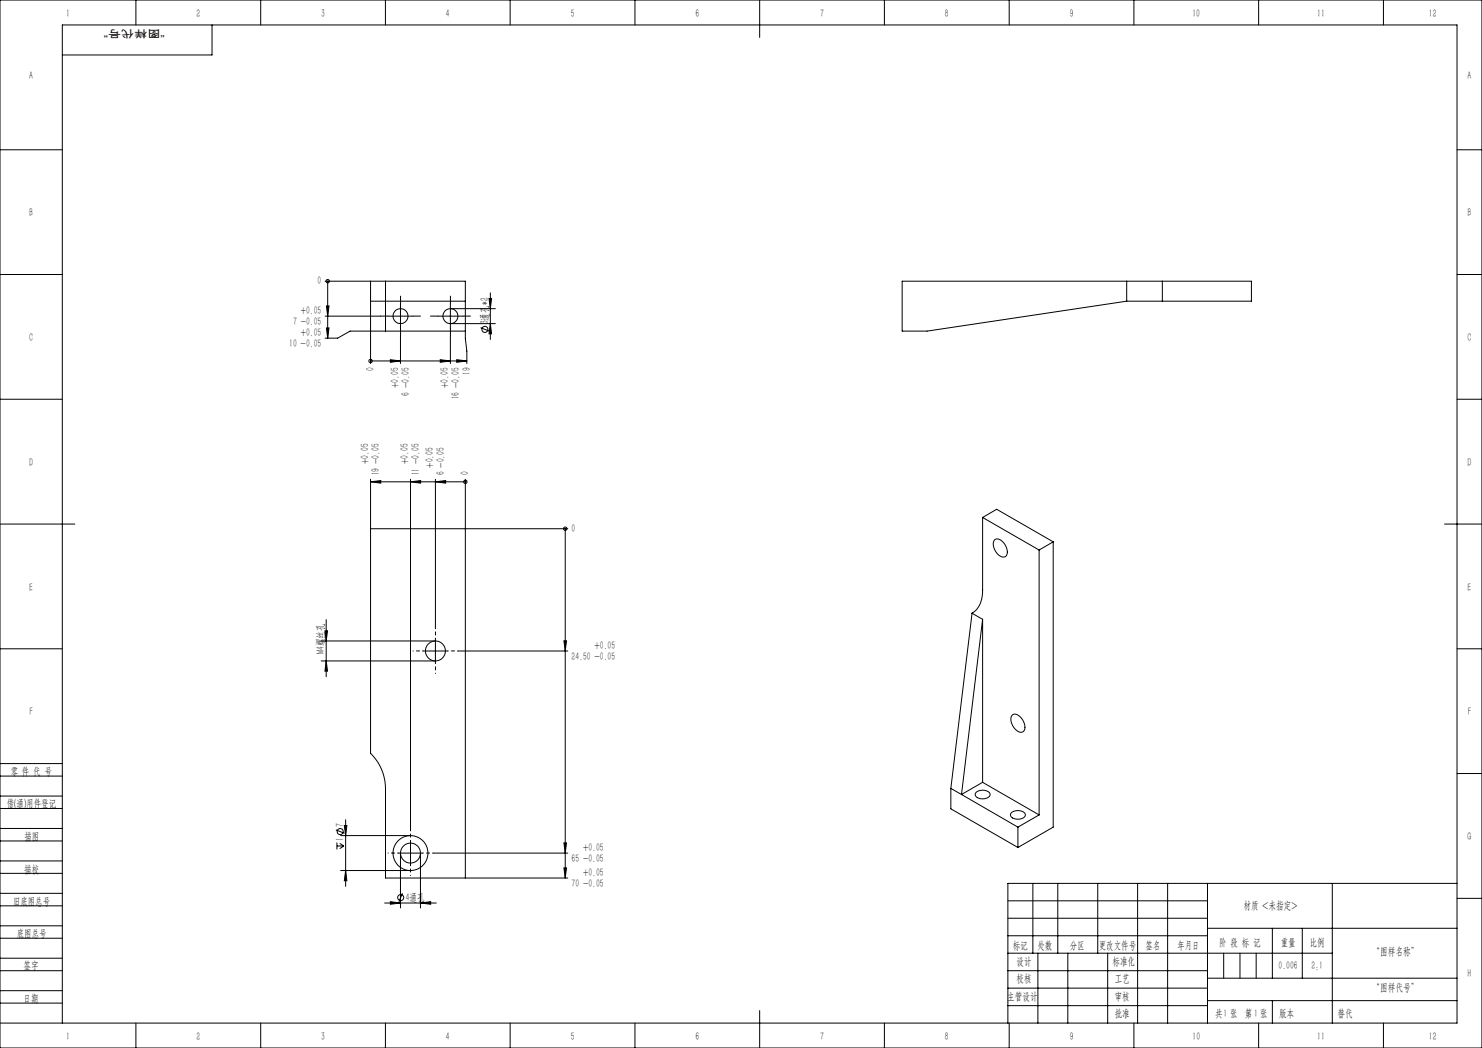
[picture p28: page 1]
0.05 M4螺丝孔

材质 <未指定>

阶 段 标 记 | 重量 | 比例 | “图样名称”

标记 | 处数 | 分区 | 更改文件号 | 签名 | 年月日
设计 | | | 标准化 | | | 0.006 | 2:1
校核 | | | 工艺

“图样代号”

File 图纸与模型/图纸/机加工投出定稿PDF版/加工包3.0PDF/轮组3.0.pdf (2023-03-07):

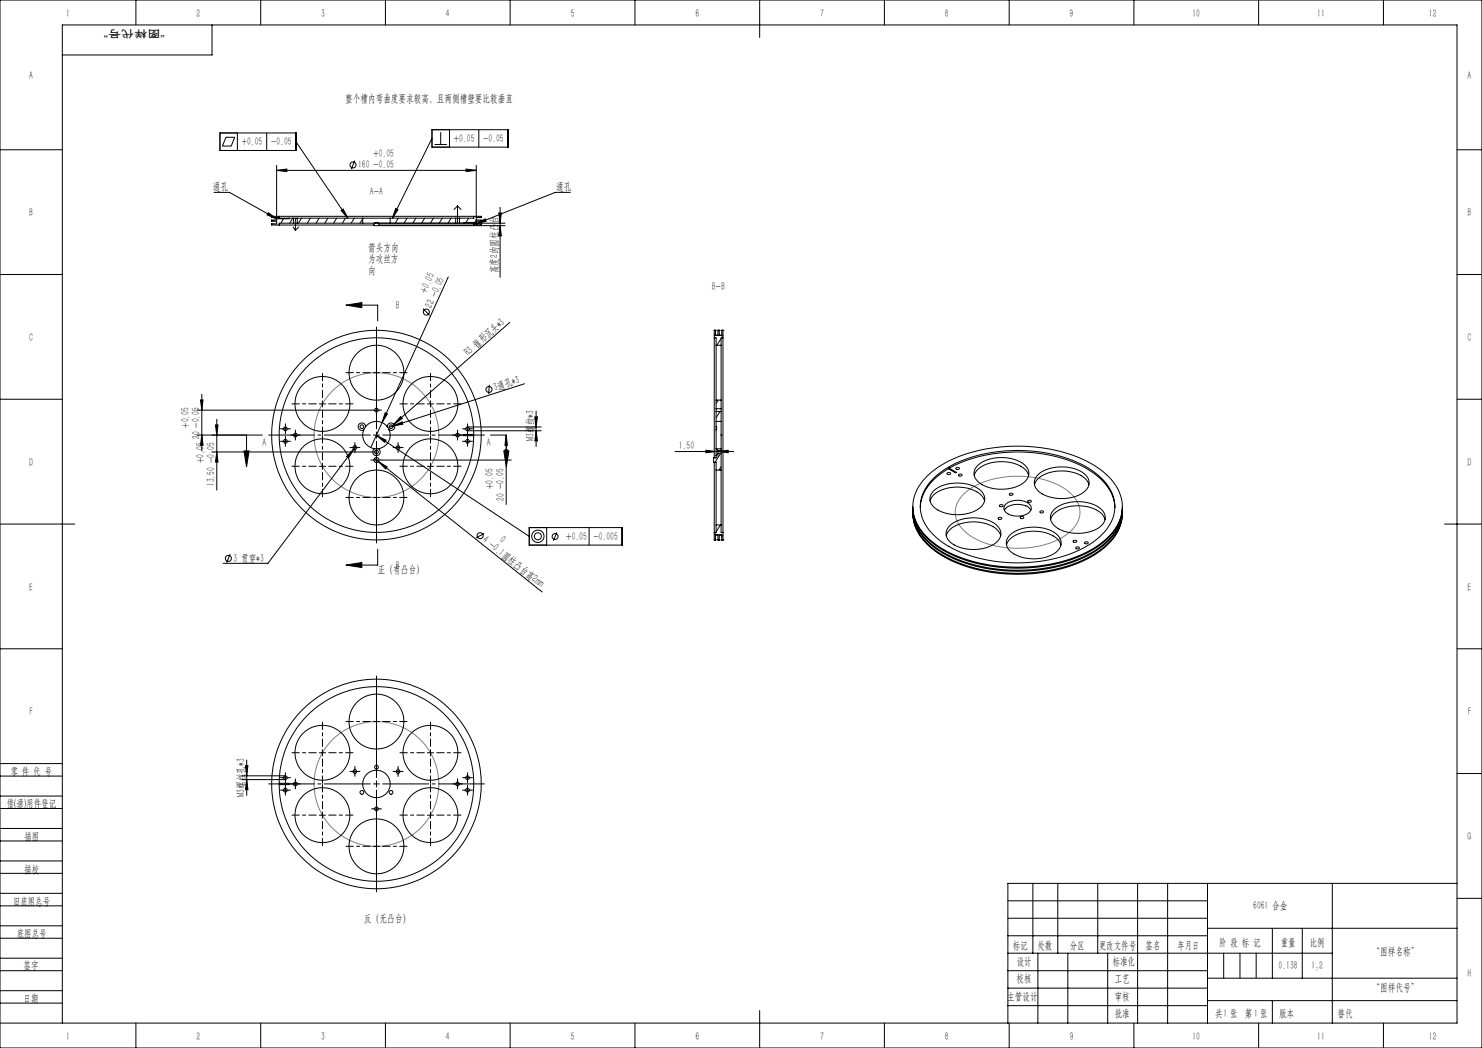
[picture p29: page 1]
00.1圆柱凸台高2mm M3螺纹*3; R3 锥形沉头*3 3通孔*3; BB 正（有凸台）; 为攻丝方 向

阶 段 标 记 | 重量 | 比例 | “图样名称”

标记 | 处数 | 分区 | 更改文件号 | 签名 | 年月日
设计 | | | 标准化 | | | 0.138 | 1:2
校核 | | | 工艺

“图样代号”

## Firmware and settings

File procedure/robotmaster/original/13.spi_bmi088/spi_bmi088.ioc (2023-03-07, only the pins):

Mcu.UserName=STM32F407IGHx
PA13.Signal=SYS_JTMS-SWDIO
PA14.Signal=SYS_JTCK-SWCLK
PA4.GPIO_Label=CS1_ACCEL
PA4.Signal=GPIO_Output
PA7.Signal=SPI1_MOSI
PB0.GPIO_Label=CS1_GYRO
PB0.Signal=GPIO_Output
PB3.Signal=SPI1_SCK
PB4.Signal=SPI1_MISO
PC4.GPIO_Label=INT1_ACCEL
PC4.Signal=GPXTI4
PC5.GPIO_Label=INT1_GRYO
PC5.Signal=GPXTI5
PF6.Signal=S_TIM10_CH1
PH0-OSC_IN.Signal=RCC_OSC_IN
PH1-OSC_OUT.Signal=RCC_OSC_OUT
